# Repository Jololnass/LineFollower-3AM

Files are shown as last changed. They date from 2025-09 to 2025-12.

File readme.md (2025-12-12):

# LineFollower

Mijn linefollower werkt!



## specifications

microcontroller: ATmega32U4

motors: N20 micro metal gear motors 30:1

h-bridge: DRV8833

sensors: (HY-S301

batteries: 2x 18650 

wireless communication: HC-08

distance sensor - motors: 10mm

weight:

speed: 0.7m/s

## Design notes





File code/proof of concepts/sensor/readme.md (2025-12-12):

# Sensoren proof of concept

minimale hard- en software die aantoont dat minimaal 6 sensoren onafhankelijk van elkaar kunnen uitgelezen worden (geen calibratie, normalisatie of interpolatie). Hierbij moet een zo groot mogelijk bereik van de AD converter benut worden (indien van toepassing)

De sensormodule bestaat uit 8 sensoren die alle 8 apart meten of er wit of zwart onder hun staan.
Deze sensor werkt het best op 3mm afstand van het te mten oppervlak.

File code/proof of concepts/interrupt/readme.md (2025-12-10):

# start/stop interrupt proof of concept
Dit is een simpele minimale code die aantoont hoe da een toggle functie kan geprogrammeerd worden met een knop en led. Uitgangen zijn gekozen a.d.h.v. het elektronisch schema.

De knop wordt uitgelezen en zal een bool (run) op initieel op 1 zetten bij het 1ste gebruik. Bij de 2de druk, als run = 1, zal diezelfde knop run op 0 zetten waardoor de led ook zal doven.

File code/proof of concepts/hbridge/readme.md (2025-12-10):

Welkom in de readme van het H-brug gedeelte van de linefollower.

De H-brug gebruikt een DRV8833 microchip. Deze heeft op het breakoutbord 4 ingangen, 4 uitgangen, VCC, GND, EEP & ULT.

De ingangen en uitgangen spreeken opzich, zeer belangrijk bij de ingangen is dat de pwm's op de zelfde clock snelheid zitten. PWM 3, 5, 6 & 11 hebben een 8bit clocksnelheid. PWM 9 & 10 hebben een 16bit clocksnelheid. ALs 2 soorten clocksnelheden worden gebruikt zullen de motoren een verschillende snelheid hebben.

De EEP pin wordt aan de VCC (5V) van de arduino gekoppeld, dit moet zeker verbonden worden anders zal de H-brug niet werken. Als de EEP geen voeding krijgt zal de H-brug in sleep modus staan waardoor de OUT's niet zullen schakelen.

De Ult pin wordt met een pull-up weerstand geschakeld, deze dient als fout detectie. Als de H-brug normaal werkt zal deze een hoog signaal hebben waardoor de arduino een laag signaal leest. Als er een interne fout in de H-brug is zal de uitgang laag zijn waardoor de arduino een hoog signaal zal lezen. Dit zullen we a.d.h.v. een HC-05 door sturen naar een gsm.

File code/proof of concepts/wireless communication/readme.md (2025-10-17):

# draadloze communicatie proof of concept
minimale hard- en software waarmee aangetoond wordt dat duplex kan gecommuniceerd worden tussen de microcontroller en een [laptop|smartphone] (schappen wat niet past), gebruik makend van [programma] (in te vullen)
<br />
### configuratie

### opmerkingen

### gebruiksaanwijzing

#include <SoftwareSerial.h>

SoftwareSerial BTserial(10, 11); // TX, RX van de HC-05
const int led1Pin = 9;           // LED 1 (ON/OFF)
const int led2Pin = 6;          // LED 2 (PWM)

int led2Value = 128;    // Basiswaarde voor LED2 (0-255)

void setup() {
  pinMode(led1Pin, OUTPUT);
  pinMode(led2Pin, OUTPUT);

  Serial.begin(9600);
  BTserial.begin(9600);

  Serial.println("Bluetooth Dual LED control ready.");
}

void loop() {
  analogWrite(led2Pin, led2Value);
  if (BTserial.available()) {
    String command = BTserial.readStringUntil('\n');
    command.trim();

    if (command.equalsIgnoreCase("ON")){
      digitalWrite(led1Pin, HIGH);
    }

    if (command.equalsIgnoreCase("OFF")){
      digitalWrite(led1Pin, LOW);
    }

    if (command.startsWith("PWM")) {
      int val = command.substring(4).toInt();
      val = constrain(val, 0, 255);
      led2Value = val; // sla waarde op zodat hij behouden blijft
    }
  }
}

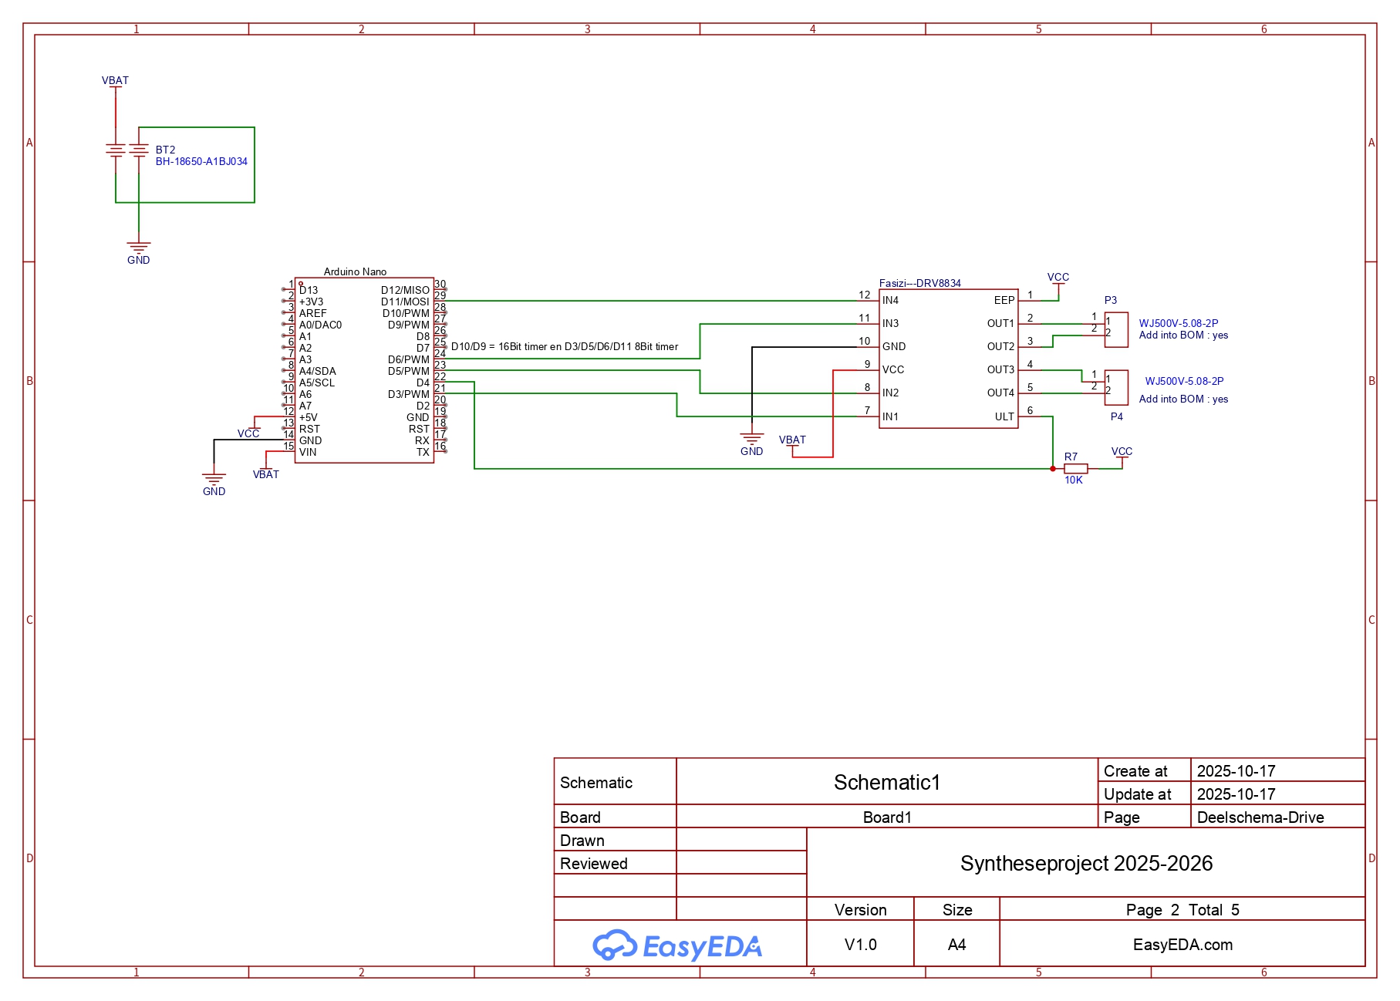
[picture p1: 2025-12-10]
code/proof of concepts/hbridge/2ce44f2f-7f96-4009-be39-690bf4bd2cc1_page-0002.jpg

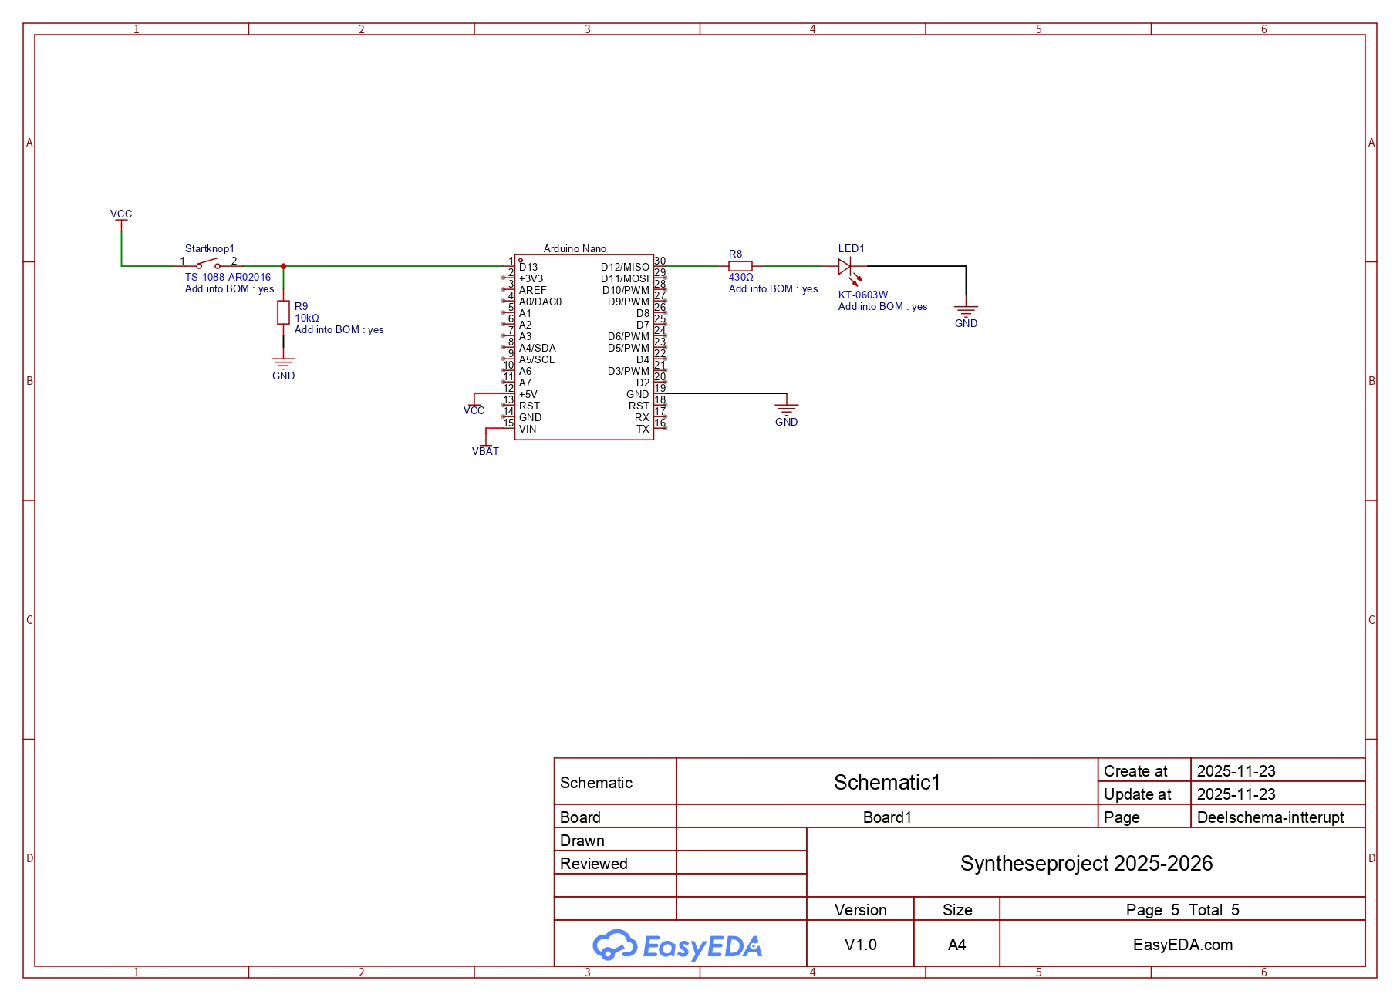
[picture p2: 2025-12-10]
code/proof of concepts/interrupt/2ce44f2f-7f96-4009-be39-690bf4bd2cc1_page-0005.jpg

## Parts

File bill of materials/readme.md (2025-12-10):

## bill of materials
<br />

|volgnummer|naam|omschrijving|nieuw/recup|kostprijs/stuk|aantal|subtotaal|
|---|---|---|---|---|---|---|
|  1|  HC-08 Bluetooth module met adapter - clone| bluetooth module | nieuw | €5.80 |  1 |  €5.80 |
|  2|  Arduino Nano R3 - kloon - met headers| Arduino Nano | nieuw | €8.60 |  1 |  €8.60 |
|  3|  Female header stackable 6 pin |5x Female headers 6 pin  nieuw |  5 |  €2.85 | 2 | €5.70 |
|  4|  Fasizi 5 x DRV8833|dubbele H-brug | nieuw | €5.99 | 1 |€5.99 |
|  5| HY-S301 | 8x IR Lijn Tracking Module | nieuw | €3.50 | 1 | €3.50 |
|  6|  Aslong JGA12-N20-30 DC-Transmissiemotor 6V - 500RPM| motor 30:1 | nieuw |  €4.50 | 2 |  €9.00 |
|  7| 15 Pins header Female | fermale headers 15 pinss | nieuw |  €0.31 | 2 | €0.62 |
|  8| 18650 | batterij | nieuw | €1.45 | 2 | €2.90 |
|  9| 2x 18650 Batterijhouder met klemkontacten en losse draden | Batterijhouder |  nieuw | €1.59 | 1 |  €1.59 |
| 10| Keeppower 2x 18650  batterijendoosje | batterijdoos | nieuw | €0.75 |1 | €0.75 |
| 11| XTAR MC2 USB-C batterijlader | batterijlader |  nieuw | €4.75 |1 | €4.75 |
| 12| | klemschroefblok 2 pins | recup | |  3 | |
| 14| Frame | Houder van alle componenten | 3D print | / | 1 | / |
| 15| Spoiler| stabiliteitsaccecoire  | 3D print | / | 1 | / |
|  TOTAALPRIJS | |Zonder verzendingskosten  | | | |  €49.2 |

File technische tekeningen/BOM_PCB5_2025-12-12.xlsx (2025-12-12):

No. | Quantity | Comment | Designator | Footprint | Value | Manufacturer Part | Manufacturer | Supplier Part | Supplier
1 | 1 | DRV8833 | Fasizi---DRV8833 | DRV8833
2 | 2 | 2.54-1*6P母 | H1,H2 | HDR-TH_6P-P2.54-V-F |  | 2.54-1*6P母 | BOOMELE(博穆精密) | C40877 | LCSC
3 | 1 | HC-05_排母*6P | HC-05 | HDR-TH_6P-P2.50-V-F-R1-C6 |  | HC-05_排母*6P |  | C9900003093 | LCSC
4 | 1 | KT-0603W | LED | LED0603-R-RD_WHITE |  | KT-0603W | KENTO | C2290 | LCSC
5 | 2 | WJ500V-5.08-2P | M-L,M-R | CONN-TH_2P-P5.00_WJ500V-5.08-2P |  | WJ500V-5.08-2P | KANGNEX(康奈克斯电气) | C8465 | LCSC
6 | 2 | 10kΩ | R1,R3 | RES-TH_BD2.7-L6.2-P10.20-D0.4 | 10kΩ | MF1/4W-10K±1%-ST52 | VO(翔胜) | C2903232 | LCSC
7 | 1 | 430Ω | R2 | RES-TH_BD1.8-L3.2-P7.20-D0.4 | 430Ω | MF1/8W-430Ω±1% T | CCO(千志电子) | C119170 | LCSC
8 | 1 | HX SS-12D10L5 | Schakelaar | SW-TH_HX-SS-12D10L5 |  | HX SS-12D10L5 | hanxia(韩下) | C42391667 | LCSC
9 | 1 | TS-1088-AR02016 | Startknop | SW-SMD_L3.9-W3.0-P4.45 |  | TS-1088-AR02016 | XUNPU(讯普) | C720477 | LCSC
10 | 1 | ABX00028 | U1 | MOD-TH_ABX00028 |  | ABX00028 | arduino | C21303176 | LCSC

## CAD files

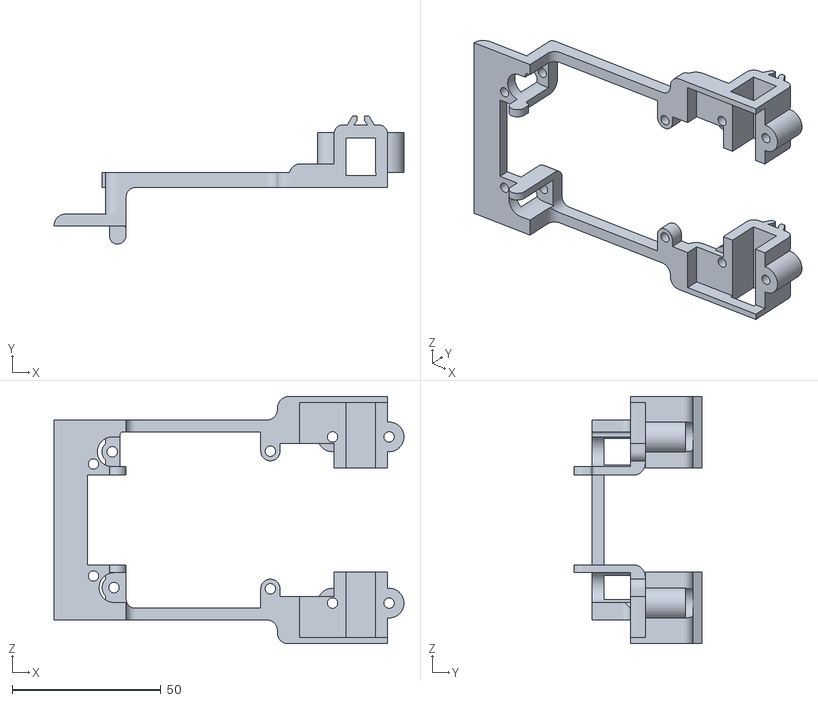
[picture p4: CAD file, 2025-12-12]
technische tekeningen/mechanisch/Frame V9.STL
117.5 x 43.0 x 83.0

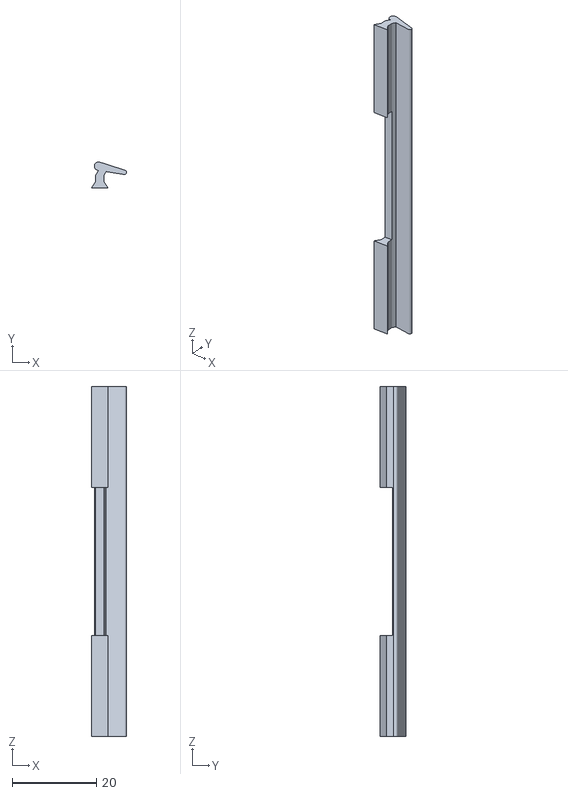
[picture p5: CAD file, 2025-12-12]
technische tekeningen/mechanisch/Spoiler_JDK.STL
8.37 x 6.20 x 83.0

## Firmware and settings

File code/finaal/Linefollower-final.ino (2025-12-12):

/*
 ----------INSTRUCTIES HOE JE DEZE CODE GEBRUIKT EN WAARDES AANPAST------------
 -----------------------------------CB-----------------------------------------
 voor de waardes intestellen (diff, power, cycle,...) stuur je in de serial monitor => "set (naam) (value)"
 voor het instellen van de cyletime stuur in de serial monitor "set cyle 1000000", cycle time voor goede werking <500
 *
 voor calibratie sensor wit stuur in serial monitor "calibrate white" ----aangeraden om voor elk gebruik opnieuw tedoen, waardes kunnen veelverschillen afhankelijk van omgeving
 voor calibratie sensor zwart stuur in serial monitor "calibrate black" ----aangeraden om voor elk gebruik opnieuw tedoen, waardes kunnen veelverschillen afhankelijk van omgeving
 *
 om de opgeslagen waarden van het eeprom geheugen te controleren stuur je in de serial monitor "debug"
 diff <0.5 anders gaat er 1 van de motoren niet achteruit!!! (fysiek motor rechts, in de programmatie is dit motor links, ben te lui om dit aantepassen)
 *
 
*/
#include "SerialCommand.h"
#include "EEPROMAnything.h"
#define SerialPort Serial
#define Baudrate 9600
bool run;  // variabele om de line follower aantezetten, zowel fysiek als via de serialmonitor
SerialCommand sCmd(SerialPort);
bool debug = false;
const int sensor[] = { A7, A6, A5, A4, A3, A2, A1, A0 };  //sensoren van links naar rechts
unsigned long previous, calculationTime;
const int led = 12;  // fysieke signalisatie om te weten of run aanstaat
long normalised[8];  //array voor de nieuwe genomaliseerde waardes
const int knop = 13;
float position;  //postie van de bay harbor speeder
int status = 0;
int index = 0;
float debugPosition;
float iTerm, lastErr;
// Motorpins
const int M1_IN1 = 3;
const int M1_IN2 = 5;
const int M2_IN3 = 11;
const int M2_IN4 = 6;
//
//
//EEPROM start
struct param_t  //dit is voor het EEPROM geheugen, deze waardes worden onthouden bij een reset
{
  unsigned long cycletime;
  int black[8];  //waarde sensor zwart
  int white[8];  //waarde sensor wit
  float Kp;
  float Ki;
  float Kd;
  float diff;
  int power;
} params;
//EEPROM stop
//
//
void setup() {
  ADCSRA &= ~((1<<ADPS2) | (1<<ADPS1) | (1<<ADPS0)); // testen, geeft extra ruis
  ADCSRA |= (1<<ADPS2); // testen, geeft extra ruis // geeft stabiele sensor waarde maar een calc time tijdens run van 792µs
  //ADCSRA = (ADCSRA & 0b11111000) | 0b010; //geeft calc tijd van 712µs maar iets minder stabiele sensor waarden 
  SerialPort.begin(Baudrate);
  sCmd.addCommand("set", onSet);
  sCmd.addCommand("debug", onDebug);
  sCmd.setDefaultHandler(onUnknownCommand);
  sCmd.addCommand("calibrate", onCalibrate);
  EEPROM_readAnything(0, params);
  SerialPort.println("ready");
  sCmd.addCommand("run", onRun);
  pinMode(led, OUTPUT);
  pinMode(knop, INPUT);
  status = LOW;
  pinMode(M1_IN1, OUTPUT);
  pinMode(M1_IN2, OUTPUT);
  pinMode(M2_IN3, OUTPUT);
  pinMode(M2_IN4, OUTPUT);
}
//
//
//
void loop() {
  Aanzetten();
  sCmd.readSerial();
  unsigned long current = micros();            // non blokking wait
  if (current - previous >= params.cycletime)  //cycletime in de params (EEPROM) omgeving
  {
    previous = current;
    //normalisatie start
    for (int i = 0; i < 8; i++) {
      long value = analogRead(sensor[i]);
      normalised[i] = map(value, params.black[i], params.white[i], 0, 1024);  //herschaling van de sensor waarden
    }
    //normalisatie einde
    //herbekijk de video interpolatie
    /*volgende code zorgt voor de interpolatie van de sensor waarde. met een bereik van 30 t.e.m. -30 */                                                                                                                                                                                                                                                                                                          if (status == 0){run = 0;}   
    //
    for (int i = 1; i < 6; i++)
      if (normalised[i] < normalised[index]) index = i;
    if (normalised[index] > 500) run = false;  //als de line-follower van de zwarte lijn is zal hij stoppen
    if (index == 0) position = -20;
    else if (index == 5) position = 20;
    else {
      int sNul = normalised[index];
      int sMinEen = normalised[index - 1];
      int sPlusEen = normalised[index + 1];
      float b = sPlusEen - sMinEen;
      b = b / 2;
      float a = sPlusEen - b - sNul;
      position = -b / (2 * a);
      position += index;
      position -= 3.5;
      position *= 15;
    }
    //
    //
    //PID
    if (run == 1)  //Voor de Iterm, zodat deze pas zal werken als de auto actief is, DUBBEL CHECKEN
    {
      debugPosition = position;
      float error = -position;
      float output = error * params.Kp;  // output berekening met Kp
      //
      //I regelaar start
      //iterm mag enkel worden uitgevoerd tijdens het rijden, anders zal deze zeer snel naar zen maximum lopen
      //
      iTerm += params.Ki * error;  // output berekening met Ki
      iTerm = constrain(iTerm, -510, 510);
      output += iTerm;  // zorgt ervoor dat de output geen sprongen maakt als ki opeens van waarde verandert
      // i regelaar einde
      //
      //d-regelaar start
      output += params.Kd * (error - lastErr);
      lastErr = error;
      //einde d-rgelaar
      //
      output = constrain(output, -510, 510);  //-510 & 510 zijn de uiterste pwm waarde met de motoren
      int powerLeft = 0;
      int powerRight = 0;

        if (output >= 0) {
          powerLeft = constrain(params.power + params.diff * output, -255, 255);  //limiteerd de uiterste pwm waarde van de motor
          powerRight = constrain(powerLeft - output, -255, 255);                  //limiteerd de uiterste pwm waarde van de motor
          powerLeft = powerRight + output;
        } else {
          powerRight = constrain(params.power - params.diff * output, -255, 255);  //limiteerd de uiterste pwm waarde van de motor
          powerLeft = constrain(powerRight + output, -255, 255);                   //limiteerd de uiterste pwm waarde van de motor
          powerRight = powerLeft - output;
        }
      analogWrite(M1_IN1, powerLeft > 0 ? powerLeft : 0);
      analogWrite(M1_IN2, powerLeft < 0 ? -powerLeft : 0);
      analogWrite(M2_IN3, powerRight > 0 ? powerRight : 0);
      analogWrite(M2_IN4, powerRight < 0 ? -powerRight : 0);
    }
    if (run == 0) { 
      digitalWrite(led, LOW);
      analogWrite(M1_IN1, LOW);
      analogWrite(M1_IN2, LOW);
      analogWrite(M2_IN3, LOW);
      analogWrite(M2_IN4, LOW);
     }
    unsigned long difference = micros() - current;                   //-----geen idee wat dit doet
    if (difference > calculationTime) calculationTime = difference;  //-----geen idee wat dit doet
  }
}
//
//
//
void onUnknownCommand(char* command)  //dit deel wordt uitgevoerd als onbekende commandos worden geschreven in de serialmonitor
{
  SerialPort.print("unknown command: \"");
  SerialPort.print(command);
  SerialPort.println("\"");
  run = false;
  
}
//
//
//
void onSet()  //dit deel wordt uitgevoerd als set wordt geschreven in de serialmonitor
{
  char* param = sCmd.next();
  char* value = sCmd.next();
  // als KI niet werkt -> if (strcmp(param, "cycle") == 0) params.cycletime = atol(value) ; //debug = false;
  //
  //KI om te testen, berekend ki a.d.h.v. eenheid per seconde (moet getest worden)
  if (strcmp(param, "cycle") == 0) {
    long newCycleTime = atol(value);
    float ratio = ((float)newCycleTime) / ((float)params.cycletime);

    params.Ki *= ratio;
    params.Kd /= ratio;

    params.cycletime = newCycleTime;
  } 
  
  else if (strcmp(param, "ki") == 0) {
    float cycleTimeInSec = ((float)params.cycletime) / 1000000;
    params.Ki = atof(value) * cycleTimeInSec;
  }
  //einde ki berekenen
  //kd
   else if (strcmp(param, "kd") == 0)
  {
    float cycleTimeInSec = ((float) params.cycletime) / 1000000;
    params.Kd = atof(value) / cycleTimeInSec;
  }
  
  //
  else if (strcmp(param, "power") == 0)
    params.power = atol(value);
  else if (strcmp(param, "kp") == 0) params.Kp = atof(value);      //Kp is een float
  else if (strcmp(param, "diff") == 0) params.diff = atof(value);  //diff is een float
  EEPROM_writeAnything(0, params);
}
//
//
//
void onDebug()  // debug, hier komen de belangrijke waarden om te debuggen
{
  SerialPort.print("cycle time: ");
  SerialPort.println(params.cycletime);

  SerialPort.print("calculation time: ");
  SerialPort.println(calculationTime);
  calculationTime = 0;

  //
  SerialPort.print("black: ");
  for (int i = 0; i < 7; i++) {
    SerialPort.print(params.black[i]);
    SerialPort.print(" ");
  }
  SerialPort.println(" ");
  //
  SerialPort.print("white: ");
  for (int i = 0; i < 7; i++) {
    SerialPort.print(params.white[i]);
    SerialPort.print(" ");
  }

  SerialPort.println(" ");
  //
  Serial.print("position: ");
  Serial.println(position);
  //
  Serial.print("run: ");
  Serial.println(run);

  SerialPort.print("Kp: ");
  SerialPort.print(params.Kp);
  SerialPort.println(" ");

  SerialPort.print("power: ");
  SerialPort.print(params.power);
  SerialPort.println(" ");

  SerialPort.print("diff: ");
  SerialPort.print(params.diff);
  SerialPort.println(" ");
  //
  //Geeft Ki terug met eenheid per sconde (moet getest worden)
  float cycleTimeInSec = ((float)params.cycletime) / 1000000;
  float ki = params.Ki / cycleTimeInSec;
  SerialPort.print("Ki: ");
  SerialPort.println(ki);
  //kd
   float kd = params.Kd * cycleTimeInSec;
  SerialPort.print("Kd: ");
  SerialPort.println(kd);
  
  //
}
//
//
//
void onCalibrate()  //calibratie voor de sensor
{
  char* param = sCmd.next();
  digitalWrite(led, HIGH);

  if (strcmp(param, "black") == 0)  //calibratie als "black" wordt geschreven
  {
    SerialPort.print("start calibrating black... ");
    for (int i = 0; i < 8; i++) params.black[i] = analogRead(sensor[i]);
    SerialPort.println("done");
  } else if (strcmp(param, "white") == 0)  //calibratie als "white" wordt geschreven
  {
    SerialPort.print("start calibrating white... ");
    for (int i = 0; i < 8; i++) params.white[i] = analogRead(sensor[i]);
    SerialPort.println("done");
  }

  EEPROM_writeAnything(0, params);
}
//
//
//
void Aanzetten() {
  if (run == false) {
    if (digitalRead(knop) == 1) {
      run = true;
      digitalWrite(led, HIGH);
    }
  }
}
//
//
//
void onRun() {
  char* parameter = sCmd.next();
  char* value = sCmd.next();
  if (strcmp(parameter, "on") == 0) {
    iTerm = 0;
    run = true;
    digitalWrite(led, HIGH);
  } else run = false;
}

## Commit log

2025-12-10 Create interrupt PoC code
2025-12-12 Create sensor PoC Code
2025-12-12 Create PCB
